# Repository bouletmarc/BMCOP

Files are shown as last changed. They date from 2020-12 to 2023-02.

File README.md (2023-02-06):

# BMCOP

The BMCOP is a Coil On Plug Project made with Arduino Nano V3 for Honda/Acura running on OBD1 ecus and with a distributor.

__*This project are still in Developpement, prototyping it is completly at your own risk!*__

# Introduction

The BMCOP need 2x Signal Inputs pins to acheive triggering all the four(4x) Coils. It require 1x ICM pulse signal (usually yellow/Green wire coming out of A20/A21 output pins on the ECU) and a pulse signal coming from the FC1 header INSIDE the ecu. You'll have to get the signal from the 3rd Pins of the FC1 Header counting from the top corner of the ECU. The FC1 Header are usually in the Top Right corner in a USDM OBD1 ECU.

# Connection wiring

- On the ECU, at the FC1 header location, connect the pin1 to 5V on the arduino
- On the ECU, at the FC1 header location, connect the pin3 to D2 on the arduino
- On the ECU, at the FC1 header location, connect the pin12 to GND on the arduino
- On the ECU, at the big connectors outputs, on the big connector A, CUT the ICM wire going to the body/engine bay and connect the wire coming from the ECU connector to D3 on the arduino
- On the Arduino, connect D8 with the ICM wire previously cut going to your body (to power the tachometer)
- On the Arduino, connect D4 with the Coil1 5v signal
- On the Arduino, connect D5 with the Coil2 5v signal
- On the Arduino, connect D6 with the Coil3 5v signal
- On the Arduino, connect D7 with the Coil4 5v signal

# Parts required to assembled the Prototype PCB

- 2x 1K Ohm 1/6W Resistor
- 4x 2N4148 Diode
- 1x Arduino Nano V3 - 5V - 16Mhz

(required ONLY for the v1.2 and older)
- 2x more 1K Ohm 1/6W Resistor
- 1x 100nF (0.1uF) Capacitor
*If you want to Power the Device with 12V:*
- 1x 78M05
- 1x 1N4002 (1N4004, 2N4148 and others diodes above 20V rating will works just as fine for a replacement!)

**In the Schematic 1N4002 take place of SS12**

# Possible Issues

__*The Project is for use at your OWN COMPLETE RISK, IT HAS NOT BEING TESTED/CONFIRMED*__

The project has been updated for the V1.3 boards, which now use a different signal for syncing coils (before it was using FC1 pin4, now i've updated the project to use FC1 pin3 signal). It has not been tested personnally since I don't have any cars/engines capable of testing the project on hands, but it should be more confident this time to works arround with it.

__*If you acheive successfull results*__

I'll surely appreciate to get informed of the changes done the the programming codes or the schematic if there is any, and if you would like, you could participate in the developpement of this project by subscribing to Github and yourself 'Push updates request' to this project! I am willing to share Open Source the project I ended up with before selling the only car I could have tested on, please be kindful and let's make this a working Open Source project together.

# BMCOP V1.3 Schematic/Diagram
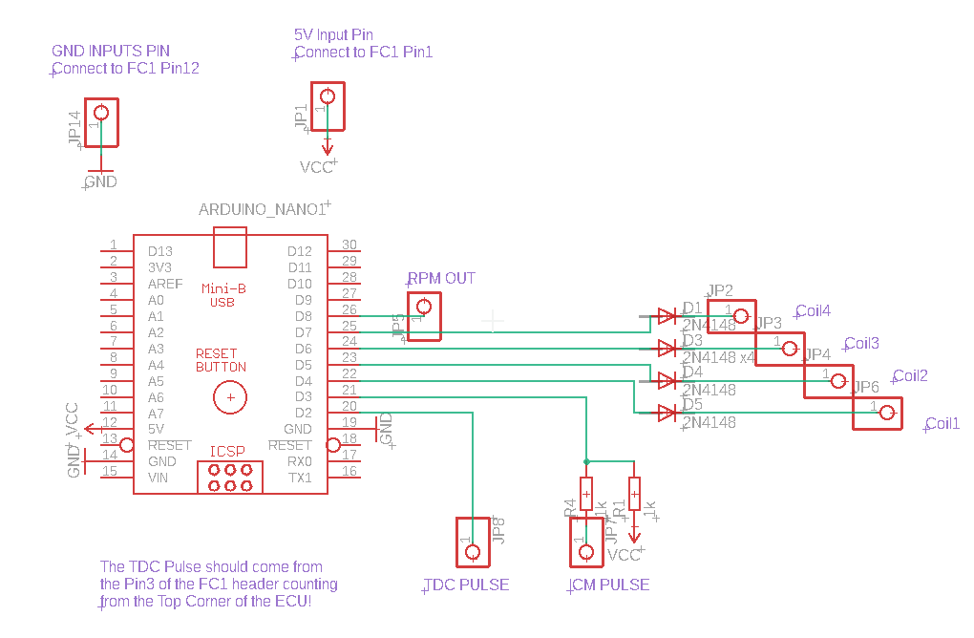
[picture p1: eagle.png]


# BMCOP V1.2 Schematic/Diagram
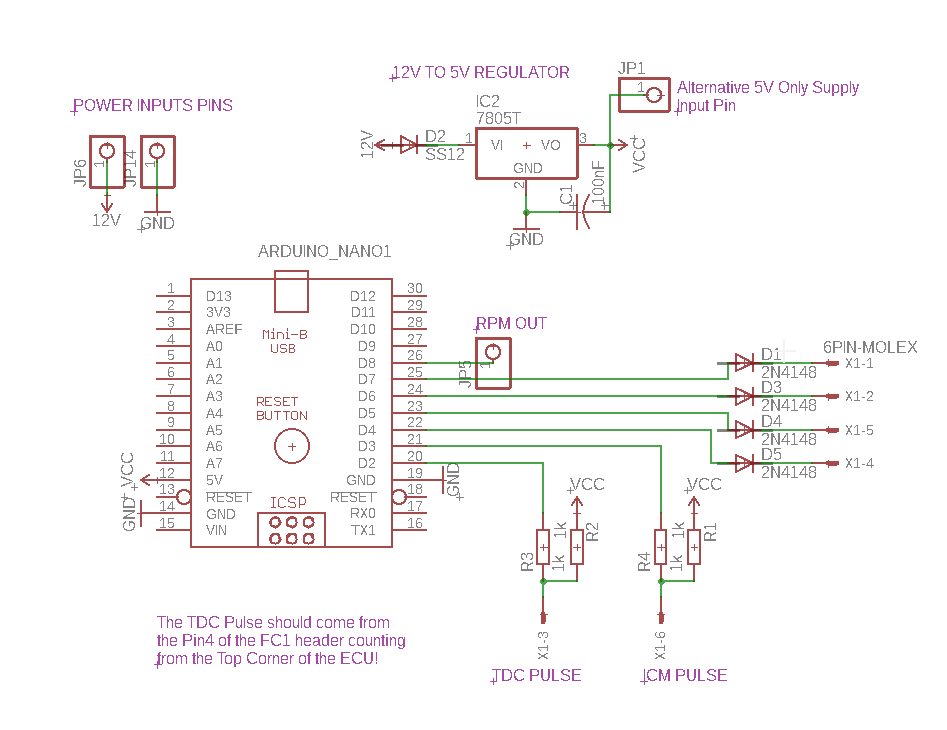
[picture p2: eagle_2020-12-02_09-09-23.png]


[Clic HERE to Check my others Products!]:<https://bmdevs.fwscheckout.com/>

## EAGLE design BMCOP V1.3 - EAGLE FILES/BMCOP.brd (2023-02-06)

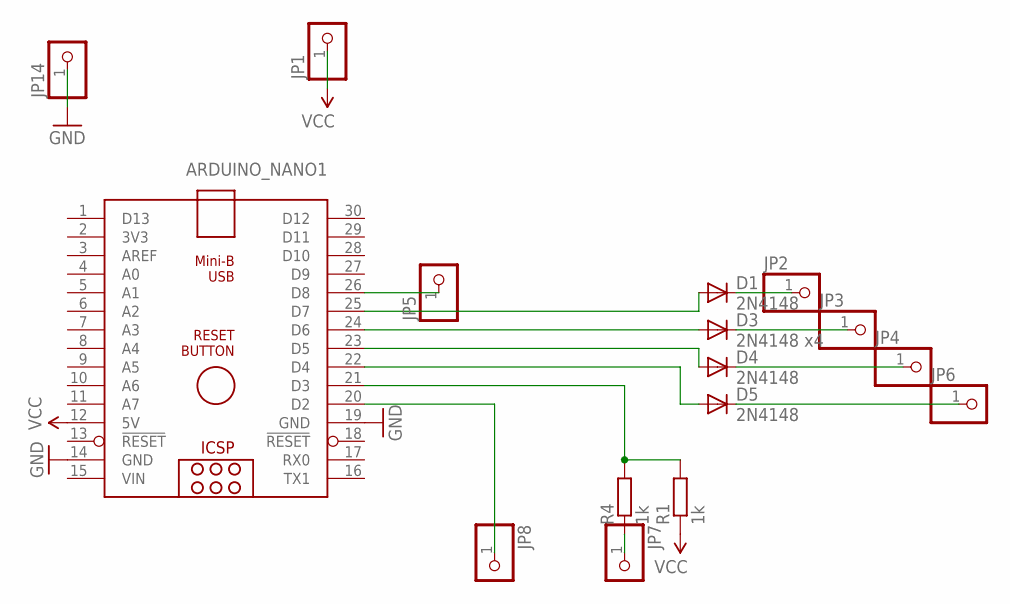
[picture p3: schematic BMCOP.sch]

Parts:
ARDUINO_NANO1: ARDUINO_NANO
D1, D4, D5: 2N4148; D-7.5
D3: 2N4148 x4; D-7.5
JP1, JP2, JP3, JP4, JP5, JP6, JP7, JP8, JP14: PINHD-1X1; 1X01
R1, R4: 1k; 0204/7

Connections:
GND: ARDUINO_NANO1.14 (GND), ARDUINO_NANO1.19 (GND), JP14.1
unnamed: ARDUINO_NANO1.25 (D7), D1.A
unnamed: ARDUINO_NANO1.24 (D6), D3.A
unnamed: ARDUINO_NANO1.23 (D5), D4.A
unnamed: ARDUINO_NANO1.22 (D4), D5.A
unnamed: ARDUINO_NANO1.26 (D8), JP5.1
unnamed: JP7.1, R4.1
unnamed: ARDUINO_NANO1.21 (D3), R1.2, R4.2
unnamed: D4.C, JP4.1
unnamed: D1.C, JP2.1
unnamed: D3.C, JP3.1
unnamed: ARDUINO_NANO1.20 (D2), JP8.1
unnamed: D5.C, JP6.1
VCC: ARDUINO_NANO1.12 (5V), JP1.1, R1.1
VIN: ARDUINO_NANO1.15 (VIN)

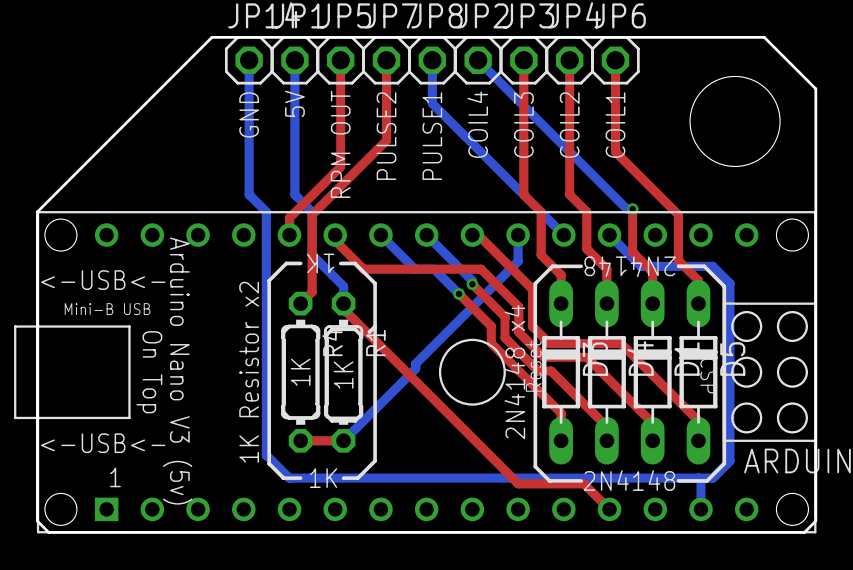
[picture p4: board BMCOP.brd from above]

Board: 2 copper layers, 43.2 x 27.5 mm, 16 parts (0 on the bottom side), 14 nets.

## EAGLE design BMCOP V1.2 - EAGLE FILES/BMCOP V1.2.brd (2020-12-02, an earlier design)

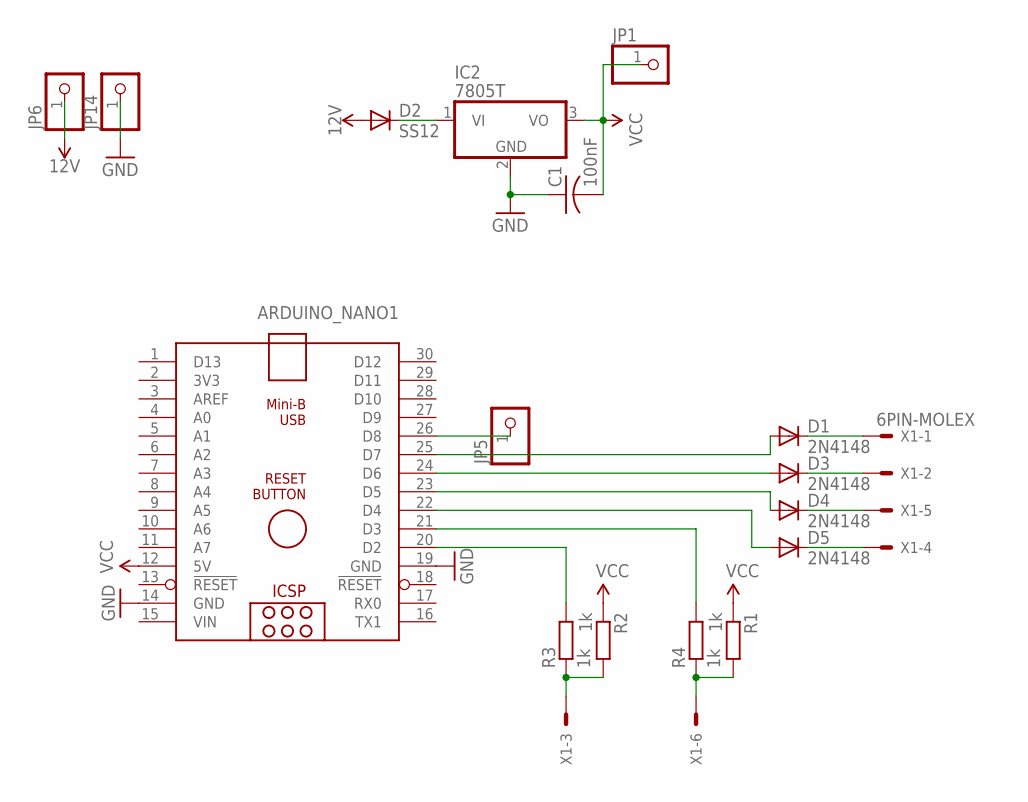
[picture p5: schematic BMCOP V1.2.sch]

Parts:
ARDUINO_NANO1: ARDUINO_NANO
C1: 100nF; C025-024X044
D1, D3, D4, D5: 2N4148; D-7.5
D2: SS12; D-7.5
IC2: 7805T; TO220H
JP1, JP5, JP6, JP14: PINHD-1X1; 1X01
R1, R2, R3, R4: 1k; 0204/7
X1: 6PIN-MOLEX

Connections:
12V: D2.A, JP6.1
GND: ARDUINO_NANO1.14 (GND), ARDUINO_NANO1.19 (GND), C1.1, IC2.2 (GND), JP14.1
unnamed: ARDUINO_NANO1.25 (D7), D1.A
unnamed: ARDUINO_NANO1.24 (D6), D3.A
unnamed: ARDUINO_NANO1.23 (D5), D4.A
unnamed: ARDUINO_NANO1.22 (D4), D5.A
unnamed: D2.C, IC2.1 (VI)
unnamed: ARDUINO_NANO1.26 (D8), JP5.1
unnamed: R1.2, R4.1, X1.6
unnamed: ARDUINO_NANO1.21 (D3), R4.2
unnamed: ARDUINO_NANO1.20 (D2), R3.2
unnamed: D4.C, X1.5
unnamed: D1.C, X1.1
unnamed: D3.C, X1.2
unnamed: R2.2, R3.1, X1.3
unnamed: D5.C, X1.4
VCC: ARDUINO_NANO1.12 (5V), C1.2, IC2.3 (VO), JP1.1, R1.1, R2.1
VIN: ARDUINO_NANO1.15 (VIN)

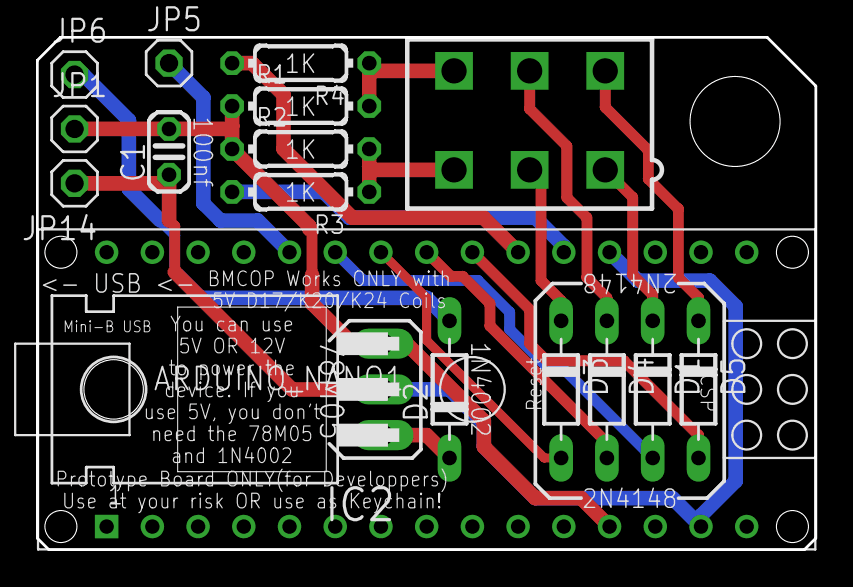
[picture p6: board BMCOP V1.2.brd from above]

Board: 2 copper layers, 43.2 x 28.5 mm, 17 parts (0 on the bottom side), 17 nets.

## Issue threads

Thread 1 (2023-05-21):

[Question] - Why are you not using opamps or similar?

sbtoonz, 2023-05-21:
Curious if the voltage coming from the arduino pins is sufficient to actually trigger the coilpacks in real life

I am coming from other coil packs (audi r8 VAG style) and they require like 4.1-5v to fire OK

Was curious about the K series ones as this project looks promising the other one I found on git has not been updated recently unsure of it's status / reliability

Closed 2023-05-23.

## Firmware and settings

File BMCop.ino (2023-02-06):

/**********************************************************************
       __________  ______      ____  _   __   ____  __    __  ________
      / ____/ __ \/  _/ /     / __ \/ | / /  / __ \/ /   / / / / ____/
     / /   / / / // // /     / / / /  |/ /  / /_/ / /   / / / / / __  
    / /___/ /_/ // // /___  / /_/ / /|  /  / ____/ /___/ /_/ / /_/ /  
    \____/\____/___/_____/  \____/_/ |_/  /_/   /_____/\____/\____/   
    
COIL ON PLUG Script V1.3 for Atmega328P made by Bouletmarc (BMDevs)

This Coil On Plug script are intended to be used on Honda/Acura 4cylinders cars running on a distributor normally. (Mostly Serie B-D-F-H Engines)

This application samples require two signals, (ICM & FC1 Pin3)
It syncs the firing sequence to the specific Cylinder from the FC1 Pin3 signal and then control the firing sequence to the coils with the ICM signal.
It activate 4x Digital ouputs pins (used to trigger each coils) depending on which cylinder should fire.

Connection wiring:
On the ECU, at the FC1 header location, connect the pin1 to 5V on the arduino
On the ECU, at the FC1 header location, connect the pin3 to D2 on the arduino
On the ECU, at the FC1 header location, connect the pin12 to GND on the arduino
On the ECU, at the big connectors outputs, on the big connector A, CUT the ICM wire going to the body/engine bay and connect the wire coming from the ECU connector to D3 on the arduino
On the Arduino, connect D8 with the ICM wire previously cut going to your body (to power the tachometer)
On the Arduino, connect D4 with the Coil1 5v signal
On the Arduino, connect D5 with the Coil2 5v signal
On the Arduino, connect D6 with the Coil3 5v signal
On the Arduino, connect D7 with the Coil4 5v signal

RPM/SYNC Informations:
-The ICM signal become High state first
-The FC1 signal will trigger 6times High-Low state
-The ICM signal become Low then rapididly High state again
-The FC1 signal will trigger 12times High-Low state
-The ICM signal become Low then rapididly High state again
-The FC1 signal will trigger 4times High-Low state
--The ICM signal become Low then rapididly High state again --> but this time it's to fire the first coil!!
-The FC1 signal will trigger 5-6times High-Low state (depending on ignition timing) between each coils firing
-The FC1 signal doesn't loose timing while under ignition cut circonstances

----------------------------------------------------------------
ICM Signal:  ____---------------_-----------------------_-------_-----------_-----------_-----------_-----------_-----------_-----------_
FC1 Signal:  ________-_-_-_-_-_-_-_-_-_-_-_-_-_-_-_-_-_-_-_-_-_-_-_-_-_-_-_-_-_-_-_-_-_-_-_-_-_-_-_-_-_-_-_-_-_-_-_-_-_-_-_-_-_-_-_-_-_-_
----------------------------------------------------------------

***********************************************************************/

#include <digitalWriteFast.h>

// MODIFIABLE PARAMETERS VARS
const bool WastedSpark          = false;        //wasted spark fire each cylinders on 2x of the 4x stroke rather than only 1x stroke
const bool InternalDWellTime    = false;        //set this to true to spark the coils with the internal DWell times or to false to use the 'external' DWell time incoming from the ICM interrupt
const int DWELL_INTERNAL        = 2500;         // DWell in Microseconds (Sparking time for coils), this value enter in count only if using the Internal DWell Time
const byte fireOrder[]          = {1, 3, 4, 2}; //Basicly the firing order 1-3-4-2 can it be offseted!  ##### {4, 2, 1, 3} ##### {3, 4, 2, 1} ##### {2, 1, 3, 4}

// MODIFIABLE OUTPUT PINS (just make sure you aren't using a pins listed in the Inputs Pins bellow
const byte CoilP1 = 4;      //Atmega328P=4  ATTiny44=3
const byte CoilP2 = 5;      //Atmega328P=5  ATTiny44=4
const byte CoilP3 = 6;      //Atmega328P=6  ATTiny44=5
const byte CoilP4 = 7;      //Atmega328P=7  ATTiny44=6
const byte RPMOut = 8;      //Atmega328P=8  ATTiny44=6
//const byte Status = 10;      //Atmega328P=10  ATTiny44=8

//#############################################################################################################
// INPUT PINS (DO NOT MODIFY, INPUT PINS ARE SPECIFIC FOR THE INTERRUPTS AND OTHER IMPORTANT FUNCTIONS)
//#############################################################################################################
const byte FC1_Pin3 = 2;         //Atmega328P=2  ATTiny44=1
const byte ICM_Pin = 3;         //Atmega328P=3  ATTiny44=2

// VARS (DO NOT MODIFY)
uint8_t CYLINDER        = 0;
bool desynced           = true;
int SyncCount           = 0;
int SyncCountICM        = 0;
int LastSyncCount       = 0;
int DesyncCount         = 0;
int SyncMode            = 0;
const int MaxDesyncTime = 500; //max desync timer in milliseconds

int LogsyncCount         = 0;

// VARS FOR RPM SERIAL LOGGING
//uint8_t SPARKS          = 0;
//uint16_t RPM            = 0;
//unsigned long LASTMILLIS = 0;

//#############################################################################################################
// SETUP/STARTING CODES
//#############################################################################################################
void setup() {
  CYLINDER = 0;

  //Set Outputs
  Ignite_Off();     //Turn Off all Coils before enabling Outputs
  pinModeFast(CoilP1, OUTPUT);
  pinModeFast(CoilP2, OUTPUT);
  pinModeFast(CoilP3, OUTPUT);
  pinModeFast(CoilP4, OUTPUT);
  pinModeFast(RPMOut, OUTPUT);
  //pinModeFast(Status, OUTPUT);

  //Set Inputs
  pinMode(FC1_Pin3, INPUT);
  pinMode(ICM_Pin, INPUT);

  //Attach Interrupts
  attachInterrupt(digitalPinToInterrupt(FC1_Pin3), ISR_FC1_Pin3, RISING);
  attachInterrupt(digitalPinToInterrupt(ICM_Pin), ISR_ICM_Pin, FALLING);

  //Set RPM Serial logging Timer
  //SetTimer();
  //Serial.begin(115200);
}

//###############################################################
// MAIN RUNNING CODES
//###############################################################
void loop() {
  delay(1);
  CalculateIsSynced();

  //Calucalute average DWell time with Engine RPM
  //DWELL_INTERNAL  = map(RPM, 0, 11000, MAXDWELL, MINDWELL);

  //Serial.println("SyncCount=" + String(SyncCount) + ", SyncCountICM=" + String(SyncCountICM) + ", LogsyncCount=" + String(LogsyncCount));
}

void CalculateIsSynced() {
  //if (!desynced) {
    if (SyncCount == LastSyncCount) {
      DesyncCount++;
    }
    if (SyncCount != LastSyncCount) {
      DesyncCount = 0;
    }
    if (DesyncCount >= MaxDesyncTime) {
      SetDecynced();
    }
    
    LastSyncCount = SyncCount;
  //}
}

void SetDecynced() {
  desynced = true;
  Ignite_Off();
  CYLINDER = 0;
  SyncCount = 0;
  SyncCountICM = 0;
  DesyncCount = 0;
  LastSyncCount = 0;
  SyncMode = 0;
}

//###############################################################
// COILS FIRING FUNCTIONS
//###############################################################
void FIRE_COIL1(){
  digitalWriteFast(CoilP1, HIGH);
  if (WastedSpark) {
    digitalWriteFast(CoilP4, HIGH);
  }
}

void FIRE_COIL2(){
  digitalWriteFast(CoilP2, HIGH);
  if (WastedSpark) {
    digitalWriteFast(CoilP3, HIGH);
  }
}

void FIRE_COIL3(){
  digitalWriteFast(CoilP3, HIGH);
  if (WastedSpark) {
    digitalWriteFast(CoilP2, HIGH);
  }
}

void FIRE_COIL4(){
  digitalWriteFast(CoilP4, HIGH);
  if (WastedSpark) {
    digitalWriteFast(CoilP1, HIGH);
  }
}

void Ignite_ON() {
  //Get the specified cylinder to fire with the firing order
  if (CYLINDER > 0) {
    //fire the desired cylinder
    if (fireOrder[CYLINDER - 1] == 1) {
      FIRE_COIL1();
    }
    if (fireOrder[CYLINDER - 1] == 2) {
      FIRE_COIL2();
    }
    if (fireOrder[CYLINDER - 1] == 3) {
      FIRE_COIL3();
    }
    if (fireOrder[CYLINDER - 1] == 4) {
      FIRE_COIL4();
    }

    //Fire ICM Out for Tachometer
    digitalWriteFast(RPMOut, LOW);
  }
}

void Ignite_Off() {
  //Turn off All Coils
  digitalWriteFast(CoilP1, LOW);
  digitalWriteFast(CoilP2, LOW);
  digitalWriteFast(CoilP3, LOW);
  digitalWriteFast(CoilP4, LOW);
  digitalWriteFast(RPMOut, HIGH);
}

//###############################################################
// INTERRUPTS FC1 AND ICM INPUTS
//###############################################################
void ISR_FC1_Pin3() {
  SyncCount++;
    
  if (!desynced)
  {
    //Increase Cylinder firing on the 5th FC1 pulse, prepare it for when the next ICM pulse will fire.
    //If the ignition degree are negative, the ICM will pulse slightly before the 6th FC1 pulse, better prepare it in advance on the 5th pulse!
    if (SyncCount == 5)
    {
      CYLINDER++;
      if (CYLINDER > 4) {
        CYLINDER = 1;
      }
      SyncCount = 0;
    }

    //Reset Sync Counting every 6x FC1 pulses
    if (SyncCount == 6) {
      SyncCount = 0;
    }
  }
}

void ISR_ICM_Pin() {
  //START SYNC SEQUENCE
  if (desynced)
  {
    //AFTER UNKNOWN FC1 PULSE
    if (SyncCountICM == 0 && SyncCount > 0)
    {
      SyncCountICM++;
      SyncCount = 0;
    }
    //AFTER 5-6 or 11-12x FC1 PULSE
    if (SyncCountICM == 1 && (SyncCount == 5 || SyncCount == 6 || SyncCount == 11 || SyncCount == 12))
    {
      SyncCountICM++;
      SyncCount = 0;
      if (SyncCount == 5 || SyncCount == 6) {
        SyncMode = 1;
      }
    }
    //AFTER UNKNOWN FC1 PULSE
    if (SyncMode == 0) {
      if (SyncCountICM == 2 && SyncCount > 0)
      {
        SyncCountICM++;
        SyncCount = 0;
        CYLINDER = 1;
        desynced = false;
      }
    }
    
    if (SyncMode == 1) {
      if (SyncCountICM <= 4 && (SyncCount == 5 || SyncCount == 6))
      {
        SyncCountICM++;
        SyncCount = 0;
      }
      if (SyncCountICM == 5 && SyncCount > 0) {
        SyncCountICM++;
        SyncCount = 0;
        CYLINDER = 1;
        desynced = false;
      }
    }
  }
  
  if(!desynced) {
    //Fire the specific Cylinder Coil
    Ignite_ON();

    //Wait for DWell Time
    if (InternalDWellTime) {
      delayMicroseconds(DWELL_INTERNAL);
    }
    else {
      while (digitalRead(ICM_Pin) == LOW) {};
    }

    //Unfire the Coils
    Ignite_Off();
  }
}



//#############################################################################################################
//#############################################################################################################
//#############################################################################################################
//#############################################################################################################
//#############################################################################################################
// RPM SERIAL LOGGING CODES
//#############################################################################################################
/*void SetTimer() {
  cli();//stop interrupts

  //set timer1 interrupt at 5Hz
  TCCR1A = 0;// set entire TCCR1A register to 0
  TCCR1B = 0;// same for TCCR1B
  TCNT1  = 0;//initialize counter value to 0

  //################################################
  // set compare match register for 1hz increments
  //Formula : ((Clock) / (Prescalar * desired interrupt frequency))
  //          ((16,000,000) / (1 * (XXX Frequency))
  //          ((16*10^6)) / (1*1024) - 1 (must be <65536)
  //################################################
  uint16_t FreqHZ = 5;  //frequency in Hz
  OCR1A = ((16000000) / (1*(FreqHZ * 1024))) - 1;
  
  // turn on CTC mode
  TCCR1B |= (1 << WGM12);
  // Set CS10 and CS12 bits for 1024 prescaler
  TCCR1B |= (1 << CS12) | (1 << CS10);  
  // enable timer compare interrupt
  TIMSK1 |= (1 << OCIE1A);
  
  sei();//allow interrupts
}

//###############################################################
ISR(TIMER1_COMPA_vect) {
  //Turn off interrupts since we use Serial commands, this also ensure we calculate the RPM when nothing trigger the interrupts (interrupts turned off)
  noInterrupts();

  //GetRPM();
  //Serial.println("RPM: " + String(RPM) + "rpm");
  Serial.println("SyncCount=" + String(SyncCount) + ", SyncCountICM=" + String(SyncCountICM) + ", LogsyncCount=" + String(LogsyncCount));

  //Attach again the interrupts since we finished calculating RPM and possibly sending Serial datas
  attachInterrupt(digitalPinToInterrupt(FC1_Pin3), ISR_FC1_Pin3, FALLING);
  attachInterrupt(digitalPinToInterrupt(ICM_Pin), ISR_ICM_Pin, RISING);
}

void GetRPM() {
  //Calculate engine RPM
  uint16_t Thistime = millis() - LASTMILLIS;
  RPM = ((30*1000)/(Thistime)*SPARKS) / 1.666;
  
  LASTMILLIS = millis();
  SPARKS = 0;
}*/

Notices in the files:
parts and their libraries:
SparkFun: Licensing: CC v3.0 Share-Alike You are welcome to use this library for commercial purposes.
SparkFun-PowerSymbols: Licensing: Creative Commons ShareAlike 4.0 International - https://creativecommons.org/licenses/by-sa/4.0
